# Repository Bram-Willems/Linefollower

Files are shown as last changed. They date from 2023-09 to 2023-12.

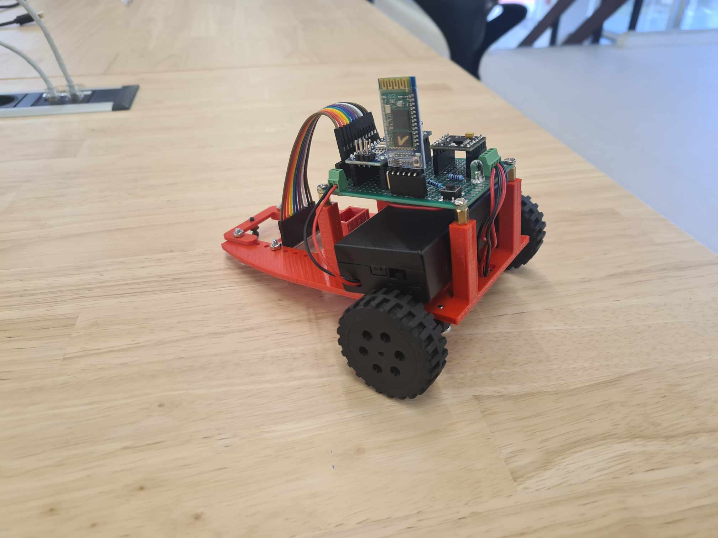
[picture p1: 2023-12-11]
images/403398465_766321181972196_1481260984969799308_n.jpg

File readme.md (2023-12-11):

# LineFollower

lege repository die je als template kan gebruiken om een eigen repository te starten voor uw linefollower project

403398465_766321181972196_1481260984969799308_n

## specifications

microcontroller:AzDilivery Nano R3 of eender welke variatie op de arduino nano

motors: 

h-bridge: DRV 8833

sensors: QTR-8A

batteries: 18650

wireless communication: HC-O5

distance sensor - motors:

weight:

speed:

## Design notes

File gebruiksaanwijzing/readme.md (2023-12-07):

# Gebruiksaanwijzing

### opladen / vervangen batterijen
De batterijen die gebruikt worden zijn 2 18650 li-ion batterijen. Deze worden opgeladen met een geschikte oplader. Om de batterijen te vervangen moet eerst de PCB van de auto worden verwijderd. Hierna kunnen de batterijen uit de houder worden gehaald en opgeladen. 

### draadloze communicatie
#### verbinding maken
Voor de draadloze communicatie wordt er gebruik gemaakt van een HC-05 bluetooth module. Op de smartphone wordt de app "Serial Bluetooth Terminal" gebruikt om verbinding te maken met de module. Hiermee kunnen de commando's worden doorgestuurd naar de arduino. 

#### commando's
debug [on/off] => Opvragen van de ingestelde parrameters. 

run  => Starten van de LineFollower. 

stop => Stoppen van de LineFollower.  

set cycle [µs]  => Instellen van de cycle time. Deze is ongeveer het dubbele van de calculation time.

set power [0..255]  => Instellen van de power van de motoren. 

set diff [0..1]  => Door de diff aan te passen zal de auto vertragen of versnellen in de bochten. Hoe hoger diff hoe meer de auto versnelt in de bochten.

set kp [0..] => Dit is de corrigatie van de fout. Hoe hoger kp hoe sterker de auto zich corrigeert om de zwarte lijn in het midden van de sensor te hebben. Als deze te hoog is zal de auto schoken van links naar rechts over de lijn.

set ki [0..] => Hoe langer de error duurt hoe sterker de linfollower zal bijsturen. 

set kd [0..] => Dit is de foutverandering. Deze kijkt naar de fout uit de vorige cyclus en gaat dan de fout bijregelen. Was deze fout groot dan wordt er meer gecorigeerd.

calibrate black => Hierdoor worden de zwarte waarden van de sensor gecalibreert.  

calibrate white => Hierdoor worden de witte waarden van de sensor gecalibreert. 

### kalibratie
Het kalibreren van de senor gebeurd met de commando's "calibrate black" en "calibrate white". Om de zwarte waarden te kalibreren moet de sensor boven een zwart oppervlak staan en dan het commando ingeven. Om de witte waarden te kalibreren gebeurd het zelfde maar op een wit oppervlak. 

### settings
De robot rijdt stabiel met volgende parameters:  

### start/stop button
Er is een start/stop button voorzien op de robot. Deze bevindt zich op de PCB, de knop is aangesloten op een intterupt pin (pin2). Deze werkt met een intterupt functie en een debounce.

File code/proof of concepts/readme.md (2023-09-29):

# Proof of Concepts

Een proof of concept is een combinatie van minimale hard- en software om eenvoudig aan te tonen dat iets werkt.  
Proof of concepts kunnen enerzijds als eerste poging dienen om een bepaald onderdeel van het project werkend te krijgen. Anderzijds kunnen ze tijdens het debuggen van het finale project dienen als test om eventuele hardware problemen te elimineren bij onduidelijke problemen.
<br />  
<br />
Een proof of concept bestaat uit
* een elektronisch schema (indien van toepassing)
* minimale code om de voorop gestelde zaken te demonstreren
* minimale uitleg / aandachtspunten
<br />
De elektronische schakelingen van de proof of concepts komen bij voorkeur overeen met deze van de uiteindelijke linefollower, zodat de code zonder aanpassingen op het finale project kan draaien.

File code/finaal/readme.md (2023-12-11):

In de ZIP-map vind je het INO-bestand met de finale code en de bijhorende bibliotheken. Houd deze samen in een mapje.

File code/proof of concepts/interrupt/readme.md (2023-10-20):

# Proof of concepts

Starten en stoppen van de robot moet ook met een fysieke monostabiele schakelaar op de robot kunnen. Deze schakelaar cyclisch gaan afvragen is geen goed idee. Dit kan enerzijds de timing van de rest van het programma in de war sturen en anderzijds riskeer je pulsen te missen. De schakelaar aan een externe interrupt van de microcontroller hangen en deze hardwarematig te bewaken is een stuk handiger.

Debouncen van de schakelaar kan je hard- of softwarematig doen. Of beide.

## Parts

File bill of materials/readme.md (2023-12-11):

## bill of materials
<br />

|volgnummer|naam|omschrijving|nieuw/recup|kostprijs/stuk|aantal|subtotaal|
|---|----|---|---|---|---|---|
|1| Microcontroller|	 AzDeilivery|	Recup|	 €0|	1|	€0|
|2|	 Sensoren| 	QTR-8A|	Nieuw|	€1,24|	1|	€1,24|
|3|	 H-brug|	 DRV8833|	Nieuw|	€0,48|	1|	€0,48|
|4|	 Motoren|Gear motor 6V 50:1|	Nieuw|	€3,25|	2| 	€6,5|
|5|	 Bluetooth|	 HC-05 module|	Nieuw|	€3,90|	1| €3,90|
|6|	 Batterij|	 18650|	Recup|	 €3,5|	  1|  	€7|
|7|	Batterij houder| 	18650 houder|	Recup| 	€0|	  1|  	€0|
|8|Batterij oplader| 18650 oplader|	Nieuw|	€3,69|	1|	€3,69|
|9|	 Weerstanden| 	 10kΩ & 220Ω|	Recup|	 €0|	2|	  €0|
|10|	 Led/knop| 	Led/knop|	Recup| 	€0|	  2|	  €0|
|11|	 Kabels|	 Kabels|	Nieuw|	€1,25|	3|	€1,25|
|12|	  Printplaaat| Printplaat plan B|	Nieuw|	€0,80|	1|	€0,80|
|13| 	Pinheaders|	 Pinheaders|	Nieuw|	€2,22|	1|	€2,22|
|14| 	Wielen|	 PLA|	Nieuw| 	 €0,5|	2| 	€1|
|15| 	Frame|	 PLA|	Nieuw|	 €1|	1|	 €1|
|  | | | | |Totaal|	  €29,08|

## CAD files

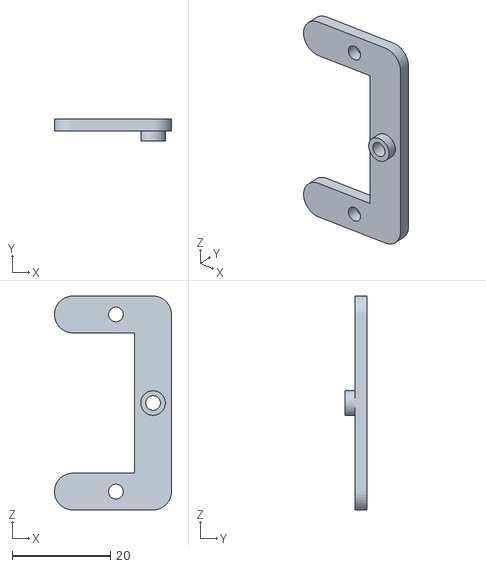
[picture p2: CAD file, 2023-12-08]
technische tekeningen/mechanisch/Sensor-plaatje.stl
23.8 x 4.50 x 43.5

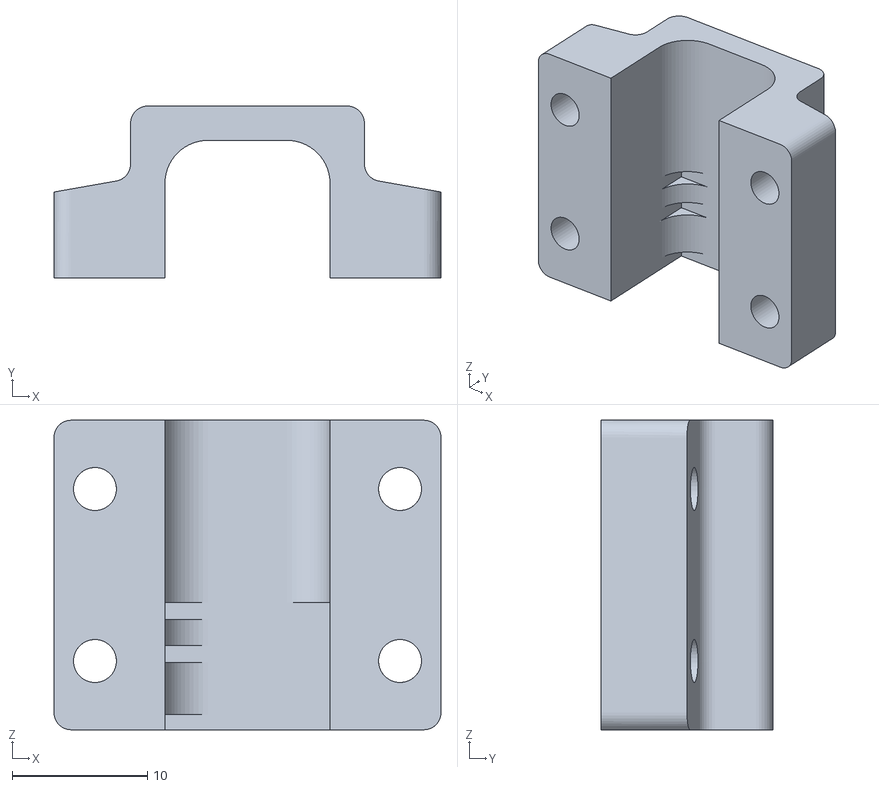
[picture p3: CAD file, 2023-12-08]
technische tekeningen/mechanisch/motor_mount_v2.1.1_straight.stl
28.6 x 12.7 x 22.9

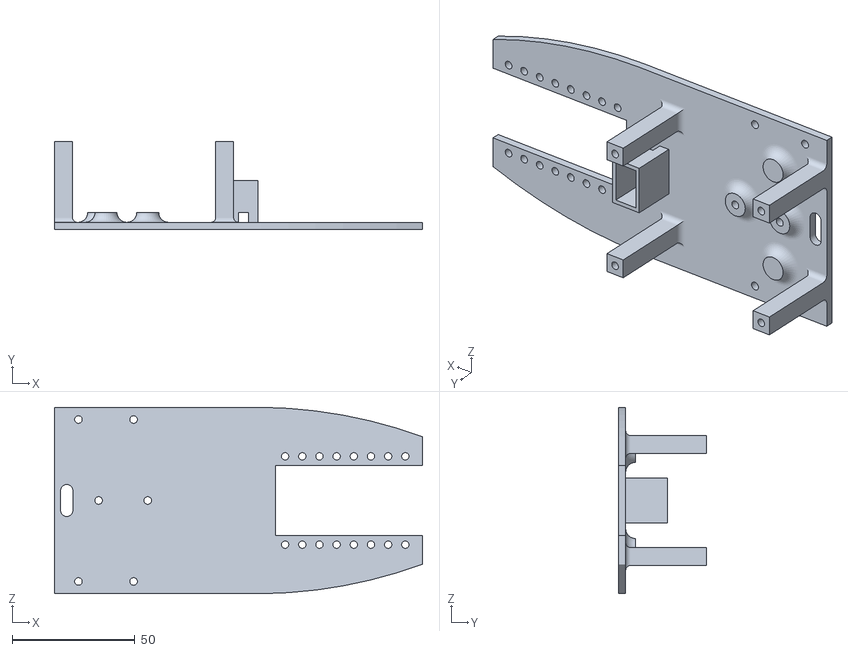
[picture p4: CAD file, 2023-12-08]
technische tekeningen/mechanisch/BaseV2.stl
150.0 x 36.0 x 76.0

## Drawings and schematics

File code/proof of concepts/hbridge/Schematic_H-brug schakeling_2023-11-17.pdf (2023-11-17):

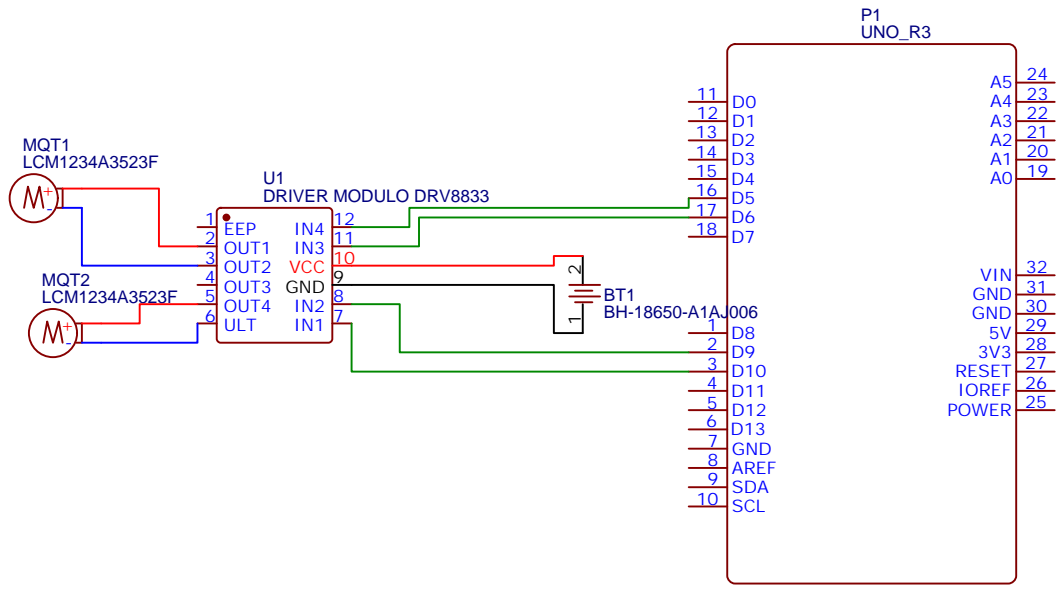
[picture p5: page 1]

POWER 25 IOREF 26 RESET 27 3V3 28 5V 29 GND 30 GND 31 VIN 32

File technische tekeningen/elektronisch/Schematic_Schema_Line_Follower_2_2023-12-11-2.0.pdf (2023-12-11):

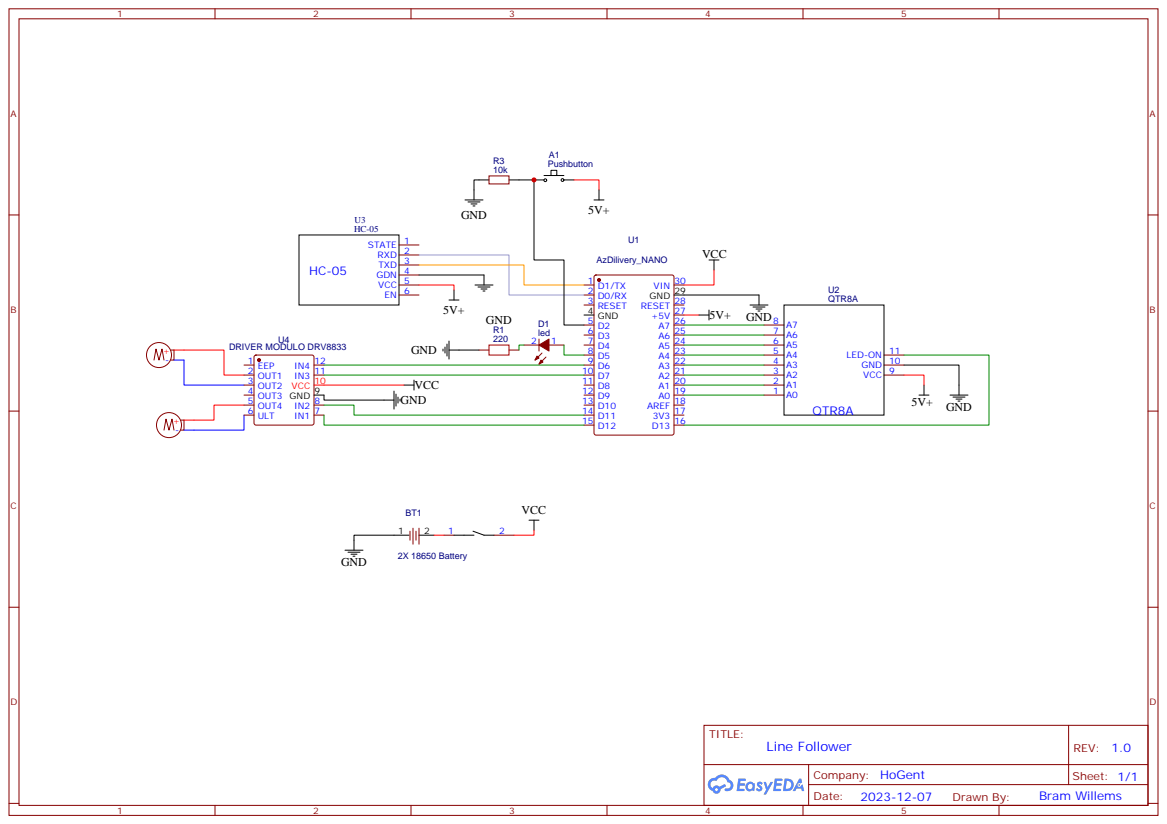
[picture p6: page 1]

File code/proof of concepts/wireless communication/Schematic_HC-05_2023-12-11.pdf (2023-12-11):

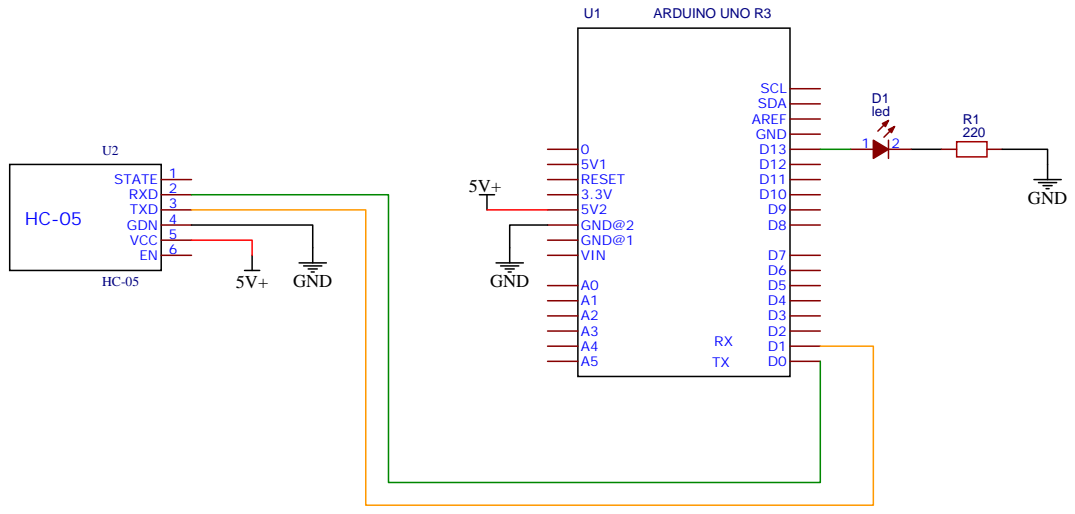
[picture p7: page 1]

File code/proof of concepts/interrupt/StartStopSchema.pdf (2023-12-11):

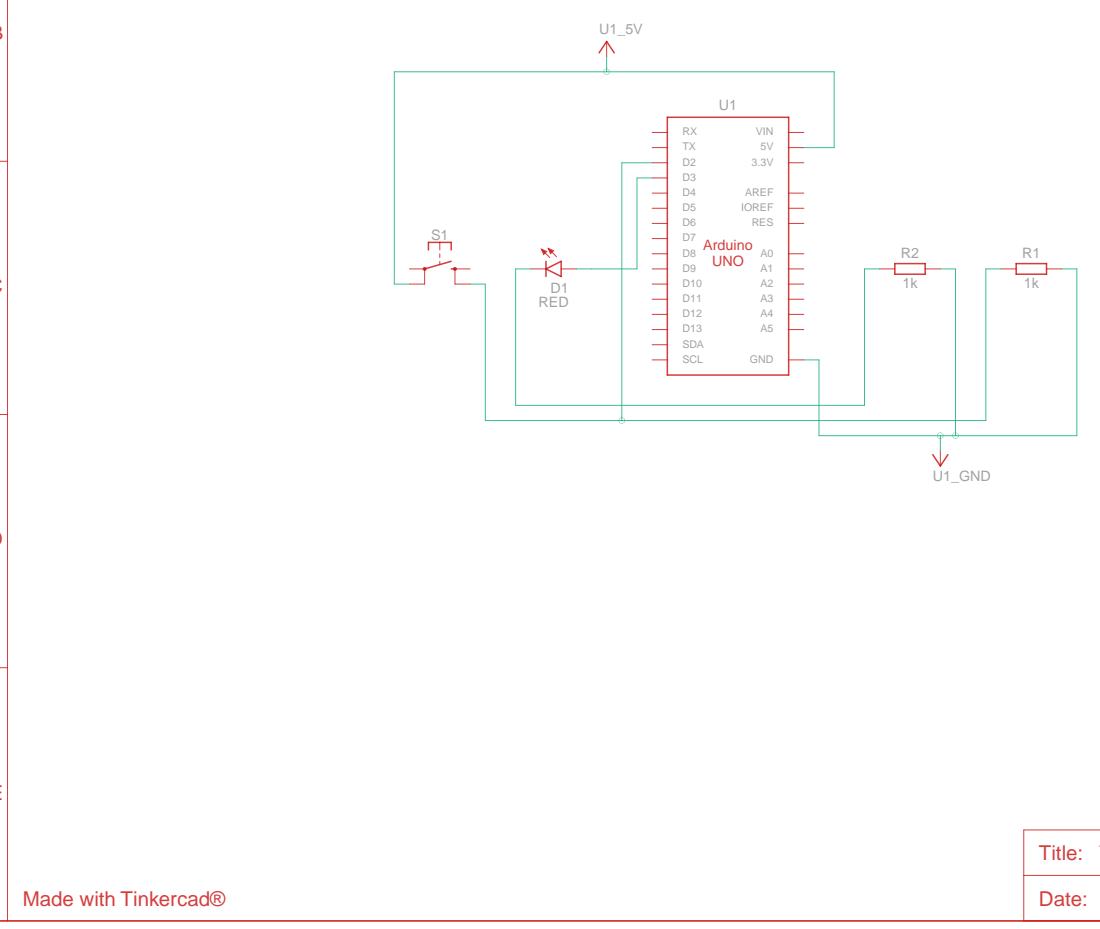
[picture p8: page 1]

Title: Tremendous Albar-Lahdi

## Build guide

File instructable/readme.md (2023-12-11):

# Instructable

Een instructable is een stappenplan - zonder verdere uitleg - hoe je vertrekkend van de bill of materials en gebruik makend van de technische tekeningen de robot kan nabouwen. Ook de nodige stappen om de microcontroller te compileren en te uploaden staan beschreven.  

### stap 1
bestel alle componenten uit de bill of materials  

### stap 2
Test aan de hand van de proof of concepts alle componenten. 
Indien nodig kan je de datasheets raadplegen

### stap 3
Nu gaan we de printplaat solderen. Hiervoor kan je het Layout schema raadplegen. 
398331318_932599908449508_257642111587116916_n
403406435_752171216730205_4686964478216439462_n

### stap 4
Het chassis kan je 3D printen. De bestanden hiervoor vind je terug onder technische tekeningen => mechanisch. Je kan ook een basisplaat maken uit bijvoorbeeld een stuk hout dat je op maat zaagt. 
Voor de wielen heb ik op zolder gezocht naar oude lego wielen en de banden hiervan gebruikt om op mijn zelf getekende wielen te plaatsen die ook ge-3Dprint zijn.

### stap 5
Om alles te monteren heb je M3-boutjes nodig. Ik zelf gebruik er met een lengte van 10mm. Voor het
Voor het monteren van de printplaat heb ik afstandsbussen gebruikt. Dit omdat de schroefdraad hiervan handig is om de printplaat meermaals te verwijderen en terug te plaatsen wat nodig is om de batterijen te kunnen opladen.
Plaats de sensor ongveer in het midden van de rij gaatjes die hiervoor voorzien zijn. Later kan je dan de afstand van de sensor ten opzichte van de wielen nog aanpassen om jouw linefollower te optimaliseren. 
393192259_1410289263242412_6914817543080417258_n
403416290_2044900662538693_571744539190810954_n
386888487_1203136880446586_7321454237098964432_n
393165127_320806970847795_4656772043914579768_n
386848513_288062390898497_2671066550627791607_n
405271464_6736014643163610_3432413520715804045_n

### stap 6
Upload het programma naar jouw arduino nano. Het programma kan je vinden onder code => finaal. Let er op dat de HC-05 module tijdens het uploaden niet verbonden is met de arduino. 

Als je al bovenstaande stappen hebt volbracht is jouw auto klaar voor gebruik. Hoe je de auto verder nog insteld en gebruikt staat uitgelegd in de gebruiksaanwijzing. 

403398465_766321181972196_1481260984969799308_n

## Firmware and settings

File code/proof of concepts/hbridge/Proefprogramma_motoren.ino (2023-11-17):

// Define the control inputs
#define MOT_A1_PIN 10
#define MOT_A2_PIN 9
#define MOT_B1_PIN 6
#define MOT_B2_PIN 5

void setup(void)
{
  // Set all the motor control inputs to OUTPUT
  pinMode(MOT_A1_PIN, OUTPUT);
  pinMode(MOT_A2_PIN, OUTPUT);
  pinMode(MOT_B1_PIN, OUTPUT);
  pinMode(MOT_B2_PIN, OUTPUT);

  // Turn off motors - Initial state
  digitalWrite(MOT_A1_PIN, LOW);
  digitalWrite(MOT_A2_PIN, LOW);
  digitalWrite(MOT_B1_PIN, LOW);
  digitalWrite(MOT_B2_PIN, LOW);

  // Initialize the serial UART at 9600 baud
  Serial.begin(9600);
}

void loop(void)
{
  // Generate a fixed motion sequence to demonstrate the motor modes.

  // Ramp speed up.
  for (int i = 0; i < 11; i++) {
    spin_and_wait(25*i, 25*i, 500);
  }
  // Full speed forward.
  spin_and_wait(255,255,2000);

  // Ramp speed into full reverse.
  for (int i = 0; i < 21 ; i++) {
    spin_and_wait(255 - 25*i, 255 - 25*i, 500);
  }

  // Full speed reverse.
  spin_and_wait(-255,-255,2000);

  // Stop.
  spin_and_wait(0,0,2000);

  // Full speed, forward, turn, reverse, and turn for a two-wheeled base.
  spin_and_wait(255, 255, 2000);
  spin_and_wait(0, 0, 1000);
  spin_and_wait(-255, 255, 2000);
  spin_and_wait(0, 0, 1000);
  spin_and_wait(-255, -255, 2000);
  spin_and_wait(0, 0, 1000);
  spin_and_wait(255, -255, 2000);
  spin_and_wait(0, 0, 1000);
}

/// Set the current on a motor channel using PWM and directional logic.
///
/// \param pwm    PWM duty cycle ranging from -255 full reverse to 255 full forward
/// \param IN1_PIN  pin number xIN1 for the given channel
/// \param IN2_PIN  pin number xIN2 for the given channel
void set_motor_pwm(int pwm, int IN1_PIN, int IN2_PIN)
{
  if (pwm < 0) {  // reverse speeds
    analogWrite(IN1_PIN, -pwm);
    digitalWrite(IN2_PIN, LOW);

  } else { // stop or forward
    digitalWrite(IN1_PIN, LOW);
    analogWrite(IN2_PIN, pwm);
  }
}

/// Set the current on both motors.
///
/// \param pwm_A  motor A PWM, -255 to 255
/// \param pwm_B  motor B PWM, -255 to 255
void set_motor_currents(int pwm_A, int pwm_B)
{
  set_motor_pwm(pwm_A, MOT_A1_PIN, MOT_A2_PIN);
  set_motor_pwm(pwm_B, MOT_B1_PIN, MOT_B2_PIN);

  // Print a status message to the console.
  Serial.print("Set motor A PWM = ");
  Serial.print(pwm_A);
  Serial.print(" motor B PWM = ");
  Serial.println(pwm_B);
}

/// Simple primitive for the motion sequence to set a speed and wait for an interval.
///
/// \param pwm_A  motor A PWM, -255 to 255
/// \param pwm_B  motor B PWM, -255 to 255
/// \param duration delay in milliseconds
void spin_and_wait(int pwm_A, int pwm_B, int duration)
{
  set_motor_currents(pwm_A, pwm_B);
  delay(duration);
}

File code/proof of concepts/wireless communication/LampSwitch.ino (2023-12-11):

int LED = 13;
char state;


void setup ()
{
  pinMode (LED, OUTPUT);
  //Serial1.begin (9600);
  Serial.begin(9600);
}

void loop()
{
  if (Serial.available())
  {
    state = Serial.read();
  }  

  if (state == '1')
    {
      digitalWrite(LED,HIGH);
      Serial.println("LEd aan");
    }
  else if (state == '0')
  {
    digitalWrite(LED,LOW);
    Serial.println("Led uit");
  }

  //Serial.println(state);
  delay(100);
}
